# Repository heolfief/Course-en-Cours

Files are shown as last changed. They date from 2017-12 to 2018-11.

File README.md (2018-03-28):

<p align="center">
	<a target="_blank" href="http://www.course-en-cours.com/">
		
	</a>

<h1 align="center">Course en cours</h1>

<p align="center">
	<a target="_blank" href="http://www.course-en-cours.com/">www.course-en-cours.com</a>
</p>
</p>
<HR>
<br>

<p align="center">
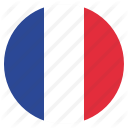
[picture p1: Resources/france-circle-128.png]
	
	<a target="_blank" href="https://github.com/heolfief/Course-en-Cours/blob/master/README_FR.md">VERSION EN FRANCAIS / FRENCH VERSION</a>
</p>

## Table of contents

- [Description](#description)
- [Where to start](#where-to-start)
- [Hardware](#hardware)
- [Software](#software)
- [Creators](#creators)
- [Copyright and license](#copyright-and-license)

## Description

This project contains hardware, software and documentation files for the "course en cours" **educationnal competition in France**.
During a year, teams of 4 to 6 middle/high school **students build their small electic car** using the same tools as engineers. the contest consists of **designing, creating, testing and running** a small model car during the **regional competitions**, to acces the **national final**.

We are two university students in electrical engineering and industrial data processing, from <a href="https://iut-rennes.univ-rennes1.fr/les-6-departements/genie-electrique-informatique-industrielle">IUT de Rennes</a>, France.
Our project is to **integrate embedded telemetry, datalogging and manual control** into the existings cars engines.
We choosed to works with the **Arduino environnement**, to make it possible for everybody to program their car, modify it as they like, and to make programming accesible for the young people of the competition.

This project is **realesed under the general public license and is strongly welcome to modifications**.

## Where to start

In order to be able to program your board with the arduino IDE via usb, you will first need to install a bootloader on your board. Find insruction on how to do that in the <a href="#bootloader">software section</a>.

When this step is done you should be able to programm your board like if it was an arduinon pro mini.

Just install the course-en-cours library (<a href="#software">link in the software section</a>) and import it to your arduino sketch.
<a target="_blank" href="https://www.arduino.cc/en/Guide/Libraries">Here is a tutorial</a> if you need help for this step.

You should now be able to program your board via USB, as described in the <a href="#software">software section</a>.

## Hardware

The hardware is based on 4 main components:
- ATmega328p microcontroller (the same as the arduino uno/nano/pro mini)
- MPU6050 accelerometer and gyro chip
- A FTDI chip (to program the microcontroller via USB)
- A micro SD card holder

This board is **fully arduino compatible** and should be selected in the arduino environnement as the arduino pro mini (ATmega328p, 3.3V 8MHz).

### Documents availables

- <a target="_blank" href="https://github.com/heolfief/Course-en-Cours/blob/master/Hardware/Schematics.pdf">Schematics (PDF)</a>
- <a target="_blank" href="https://github.com/heolfief/Course-en-Cours/blob/master/Hardware/BOM.pdf">Bill of materials (PDF)</a>
- <a target="_blank" href="https://github.com/heolfief/Course-en-Cours/blob/master/Hardware/Carte%20course%20en%20cours.sch">Autodesk Eagle schematics file</a>
- <a target="_blank" href="https://github.com/heolfief/Course-en-Cours/blob/master/Hardware/Carte%20course%20en%20cours.brd">Autodesk Eagle board file</a>
- <a href="https://github.com/heolfief/Course-en-Cours/blob/master/Hardware/Gerbers.zip">Gerber files</a>

### Board form factor
<table border="0">
	<tbody>
		<tr>
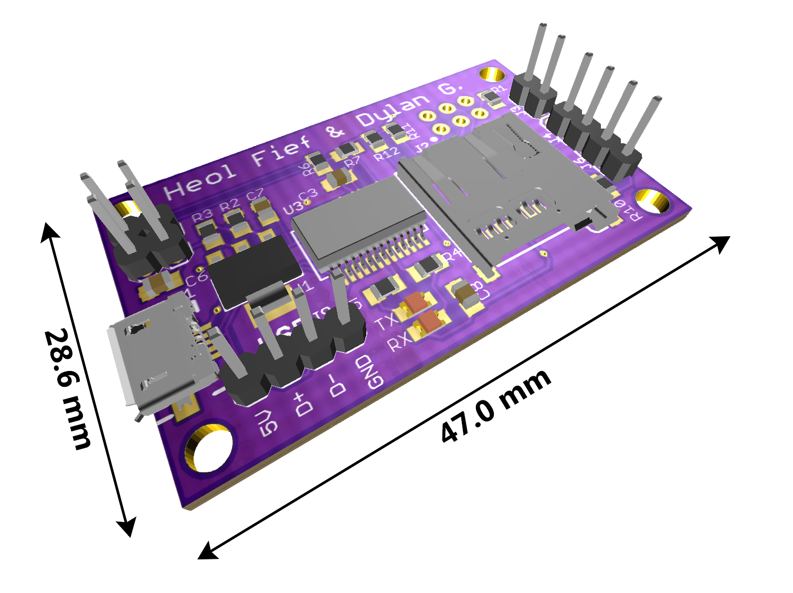
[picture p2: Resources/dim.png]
			<th align="center"></th>
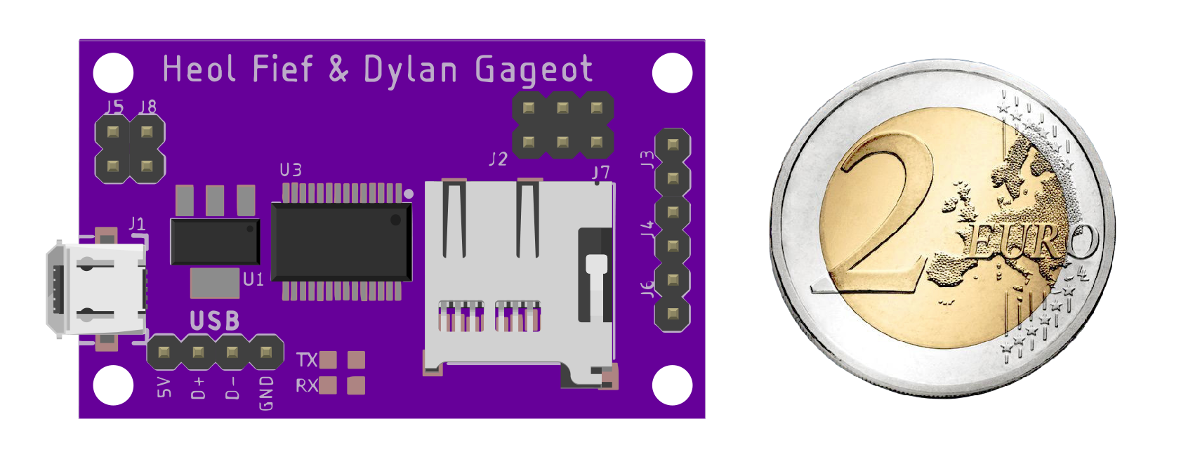
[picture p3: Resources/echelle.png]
			<th align="center"></th>
		</tr>
	</tbody>
</table>

### PCB pinout diagram:
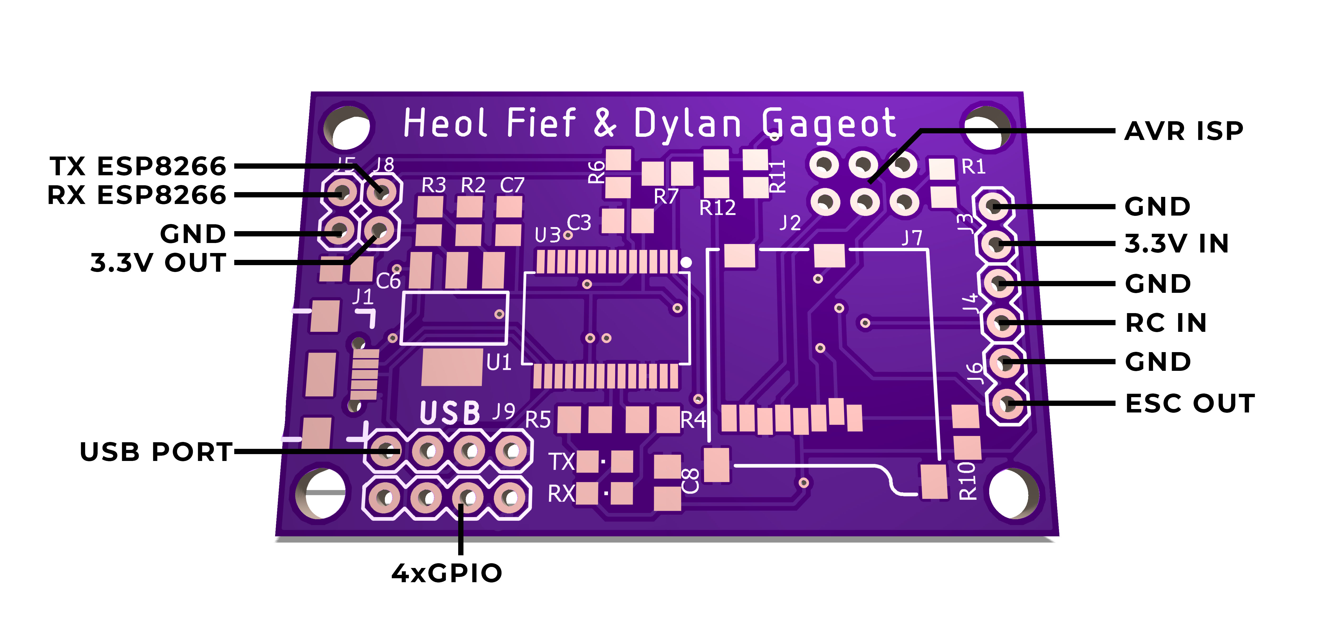
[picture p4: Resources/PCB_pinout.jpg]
PCB pinout


### PCB wiring diagram:
<p align="center">
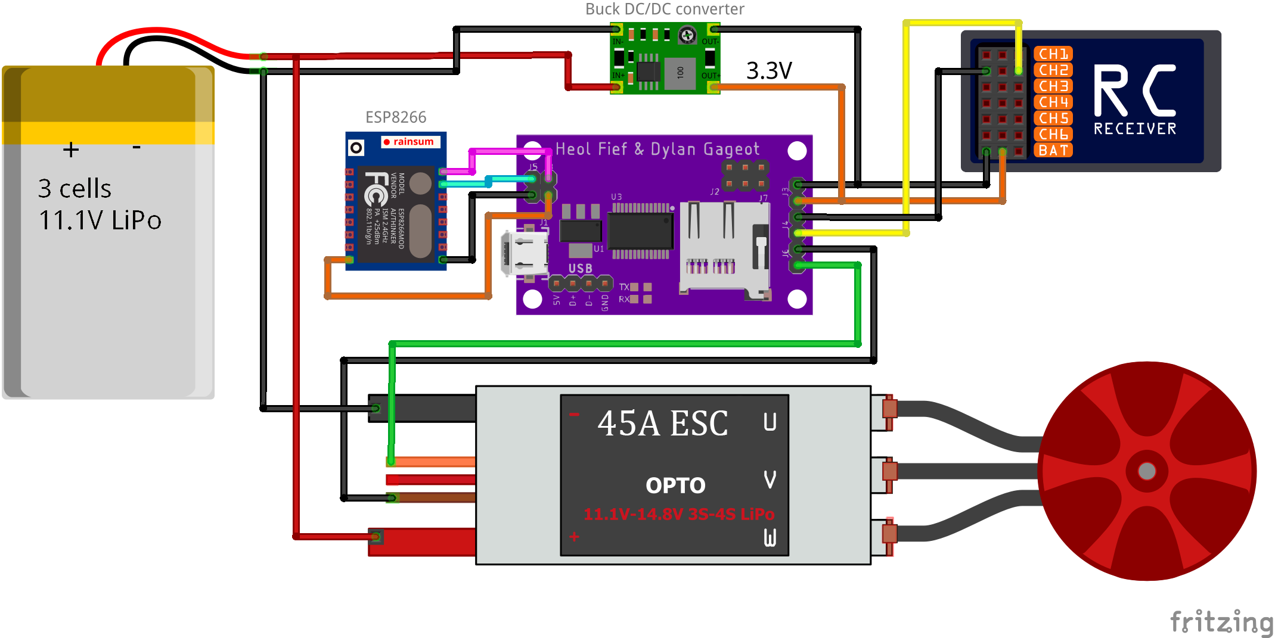
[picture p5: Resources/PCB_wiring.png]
  
</p>

**BE CAREFULL: You need to provide 3.3V to the board, plugging directly the 11.1V LiPo battery will kill it. You can step down the battery voltage with a standard DC/DC converter (also known as buck-converter) set to output 3.3V (min 200mA), like in the wiring diagram above.**

## Software

### Firmware


You can program your course en cours board in C/C++ directly with the <a target="_blank" href="https://www.arduino.cc/en/main/software">arduino IDE</a> via USB, assuming you already have a bootloader installed on your board. Instructions on how to flash a bootloader <a href="#bootloader">below</a>.

In the arduino IDE, select the "arduino pro mini" under Tools/Board, and the ATmega328p 3.3V 8MHz under Tools/Processor. Then select the COM port (under Tools/Port) on wich the board is plugged.
To access all the course en cours related function, just import the "course_en_cours" library to your sketch.
<a target="_blank" href="https://www.arduino.cc/en/Guide/Libraries">Here is a tutorial</a> if you need help for this step.

You should now be able to program your board with the arduino software environement.

The delay() function from the Arduino IDE shouldn't be used in your program because it will block the process of our library.

#### Needed libraries

- [MPU6050](https://github.com/jarzebski/Arduino-MPU6050) by **_jarzebski_** : Allows us to use the IMU.
- [SDFat](https://github.com/greiman/SdFat) by **_greiman_** : Allows us to get a high speed SD card communication.

#### Exemple code:
```cpp
#include "Course_en_Cours.h"

Couse_en_Cours cec;	 // create Couse_en_Cours object

void setup() {
	cec.initialiser(AUTO);
	cec.palier_moteur(1000,0);
	cec.palier_moteur(5000,50);
	cec.palier_moteur(7500,75);
}

void loop() {
	cec.executer();
}
```
<table>
	<tbody>
		<tr>
			<th align="center">Function</th>
			<th align="center">Description</th>
			<th align="center">Parameters</th>
		</tr>
		<tr>
			<td><code>cec.executer(void);</code></td>
			<td>Mandatory function, needs to be run in the loop().</td>
			<td>
				<ul>
				<li><strong>cec</strong> : a variable of type Course_en_cours</li>
				</ul>
			</td>
		</tr>
		<tr>
			<td><code>cec.initialiser(bool pilotage_mode);</code></td>
			<td>Function to set the driving mode. Needs to be run in the setup().</td>
			<td>
				<ul>
				<li><strong>cec</strong> : a variable of type Course_en_cours</li>
				<li><strong>pilotage_mode</strong> : the mode you want your car to run in. Can be set to "AUTO" or "MANU".
					<ul>
						<li>AUTO : you can drive the motor within your arduino code with the palier_moteur function.</li>
						<li>MANU : palier_moteur functions are disabled, and remote control signal is redirected to the ESC. You can manualy drive the motors with a remote.</li>
					</ul>
				</li>
				</ul>
			</td>
		</tr>
		<tr>
			<td><code>cec.palier_moteur(unsigned int ms, unsigned char pourcentage);</code></td>
			<td>The motor power step function. Use it in the setup() to set a fixed power/speed to the motor at a certain time. Can be called several times to create differents steps at different times. </td>
			<td>
				<ul>
					<li><strong>cec</strong> : a variable of type Course_en_cours</li>
					<li><strong>ms</strong> : the time in milieconds you want the function to take effect. Timer starts right after power-up.</li>
					<li><strong>pourcentage</strong> : this sets the power/speed of the motor, in percentage.</li>
				</ul>
			</td>
		</tr>
	</tbody>
</table>

#### Known issues

The actual software have some issues :
- If the .csv file is not already on the SD card, the logging would be slower than expected. Make sure that the file already exists on the card.
- The logging time may vary depending of how many steps (palier_moteur functions) you have added.
- The object Course_en_Cours must be called "cec" and declared as global variable (away from the loop() and setup(), or from any fonction).

### Bootloader

In order to be able to program your board with the arduino IDE via usb, you will first need to install a bootloader on your board. Sparkfun have made an easy to understand tutorial on how to do that here : <a target="_blank" href="https://learn.sparkfun.com/tutorials/installing-an-arduino-bootloader">Installing an arduino bootloader</a>

Here is the wiring diagram to install the bootloader with an arduino UNO (follow the sparkfun tutorial for step by step instructions).

<p align="center">
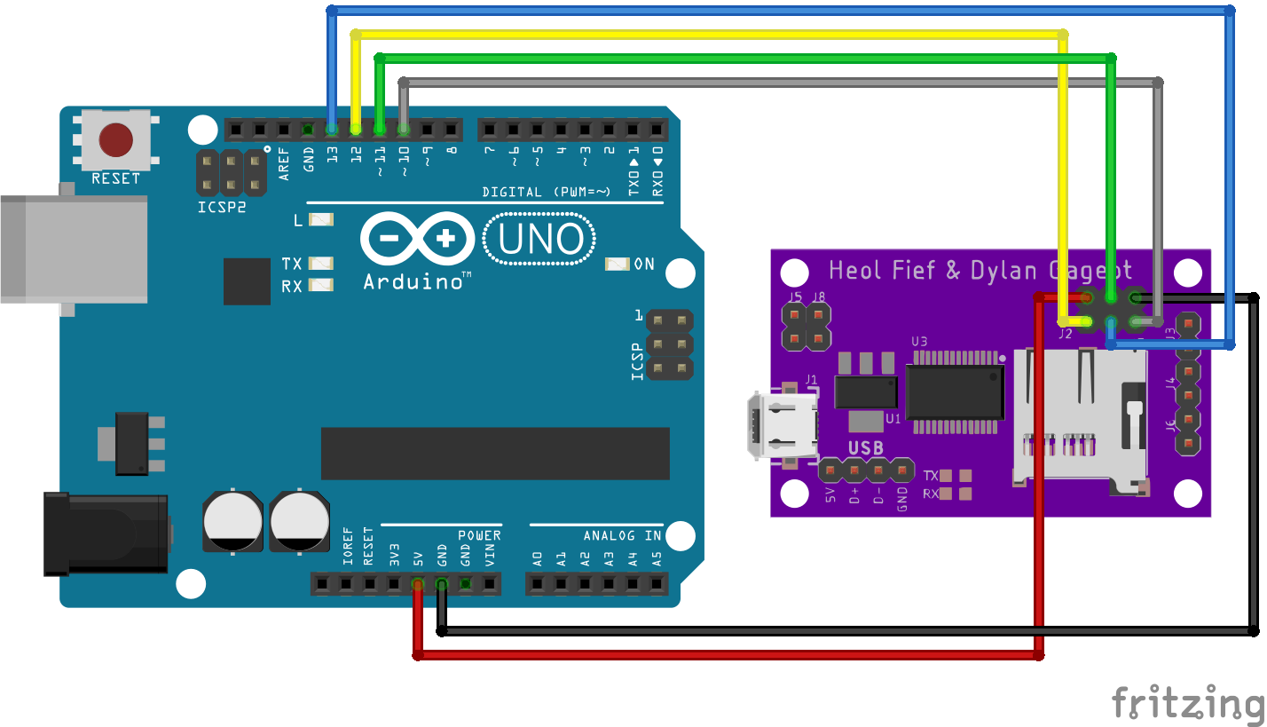
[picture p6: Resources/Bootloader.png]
  
</p>

When installing the bootloader, make sure your arduino target board is the arduino pro mini (ATmega328p 3.3V 8MHz), as this board is arduino pro mini compatible.

You should now be able to program your board via USB, as described in the <a href="#software">software section</a>.

## Creators

**Heol Fief**

- <https://github.com/heolfief>

**Dylan Gageot**

- <https://github.com/dylangageot>

## Copyright and license
heolfief/Course-en-Cours is licensed under the GNU General Public License v3.0.

See the <a target="_blank" href="https://github.com/heolfief/Course-en-Cours/blob/master/LICENSE">LICENSE file</a> for more informations.

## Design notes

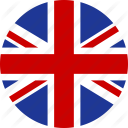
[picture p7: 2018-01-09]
Resources/england-circle-128.png

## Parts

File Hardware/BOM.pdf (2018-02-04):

Qty Value | Device | Package | Parts | Description | Price (on 100pcs order) DIGIKEY | Total price
1 | 1.6k | R-EU_R0805 | R0805 | R2 | Resistor | 0,003 € | 0,003 €
5 | 100k | R-EU_R0805 | R0805 | R1, R6, R7, R10, R11, R12 | Resistor | 0,003 € | 0,015 €
1 | 1k | R-EU_R0805 | R0805 | R3 | Resistor | 0,003 € | 0,003 €
2 | 4.7k | R-EU_R0805 | R0805 | R8, R9 | Resistor | 0,003 € | 0,006 €
2 | 330 | R-EU_R0805 | R0805 | R4, R5 | Resistor | 0,003 € | 0,006 €
6 | 100n | C-EUC0805 | C0805 | C3, C4, C5, C8, C9, C10 | Capacitor | 0,010 € | 0,060 €
1 | 10n | C-EUC0805 | C0805 | C12 | Capacitor | 0,010 € | 0,010 €
1 | 1u | C-EUC0805 | C0805 | C7 | Capacitor | 0,010 € | 0,010 €
1 | 2.2n | C-EUC0805 | C0805 | C11 | Capacitor | 0,010 € | 0,010 €
2 | 22p | C-EUC0805 | C0805 | C1, C2 | Capacitor | 0,010 € | 0,020 €
1 | 4.7u | C-EUC0805 | C0805 | C6 | Capacitor | 0,050 € | 0,050 €
2 | | LEDCHIPLED_0805 | CHIPLED_0805 | RX, TX | LED | 0,080 € | 0,160 €
1 | 8MHz | CRYSTAL-8MHZSMD-5X3.2 | CRYSTAL-SMD-5X3.2-4PAD | Y1 | 8MHz Crystal | 0,500 € | 0,500 €
1 | V_REG_317SMD | V_REG_317SMD | SOT223 | U1 | Voltage Regulator | 0,600 € | 0,600 €
1 | ATMEGA328P_TQFP | ATMEGA328P_TQFP | TQFP32-08 | U2 | Popular 328P in QFP | 1,500 € | 1,500 €
1 | FT232RL | FT232RL-BASICSSOP | SSOP28DB | U3 | FT232RL USB UART | 3,700 € | 3,700 €
1 | MPU6050 | MPU6050 | HVQFN24_NS | U4 | 6-Axis Motion Sensor | 2,920 € | 2,920 €
5 | | CONN_02 | 1X02 | J3, J4, J5, J6, J8 | Standard 0.1" header | 0,100 € | 0,500 €
1 | | CONN_04 | 1X04 | J9 | Standard 0.1" header | 0,100 € | 0,100 €
1 | | USB_MICRO-B_FEMALE-SMT | USB-B-MICRO-SMD | J1 | USB Type Micro-B Connector | 0,300 € | 0,300 €
1 | MICRO-SD_CARD_SOCKET MICRO-SD_CARD_SOCKET | MICRO-SD-SOCKET | J7 | Micro SD socket | 2,000 € | 2,000 €
| | | | | TOTAL/carte | | 12,47 €

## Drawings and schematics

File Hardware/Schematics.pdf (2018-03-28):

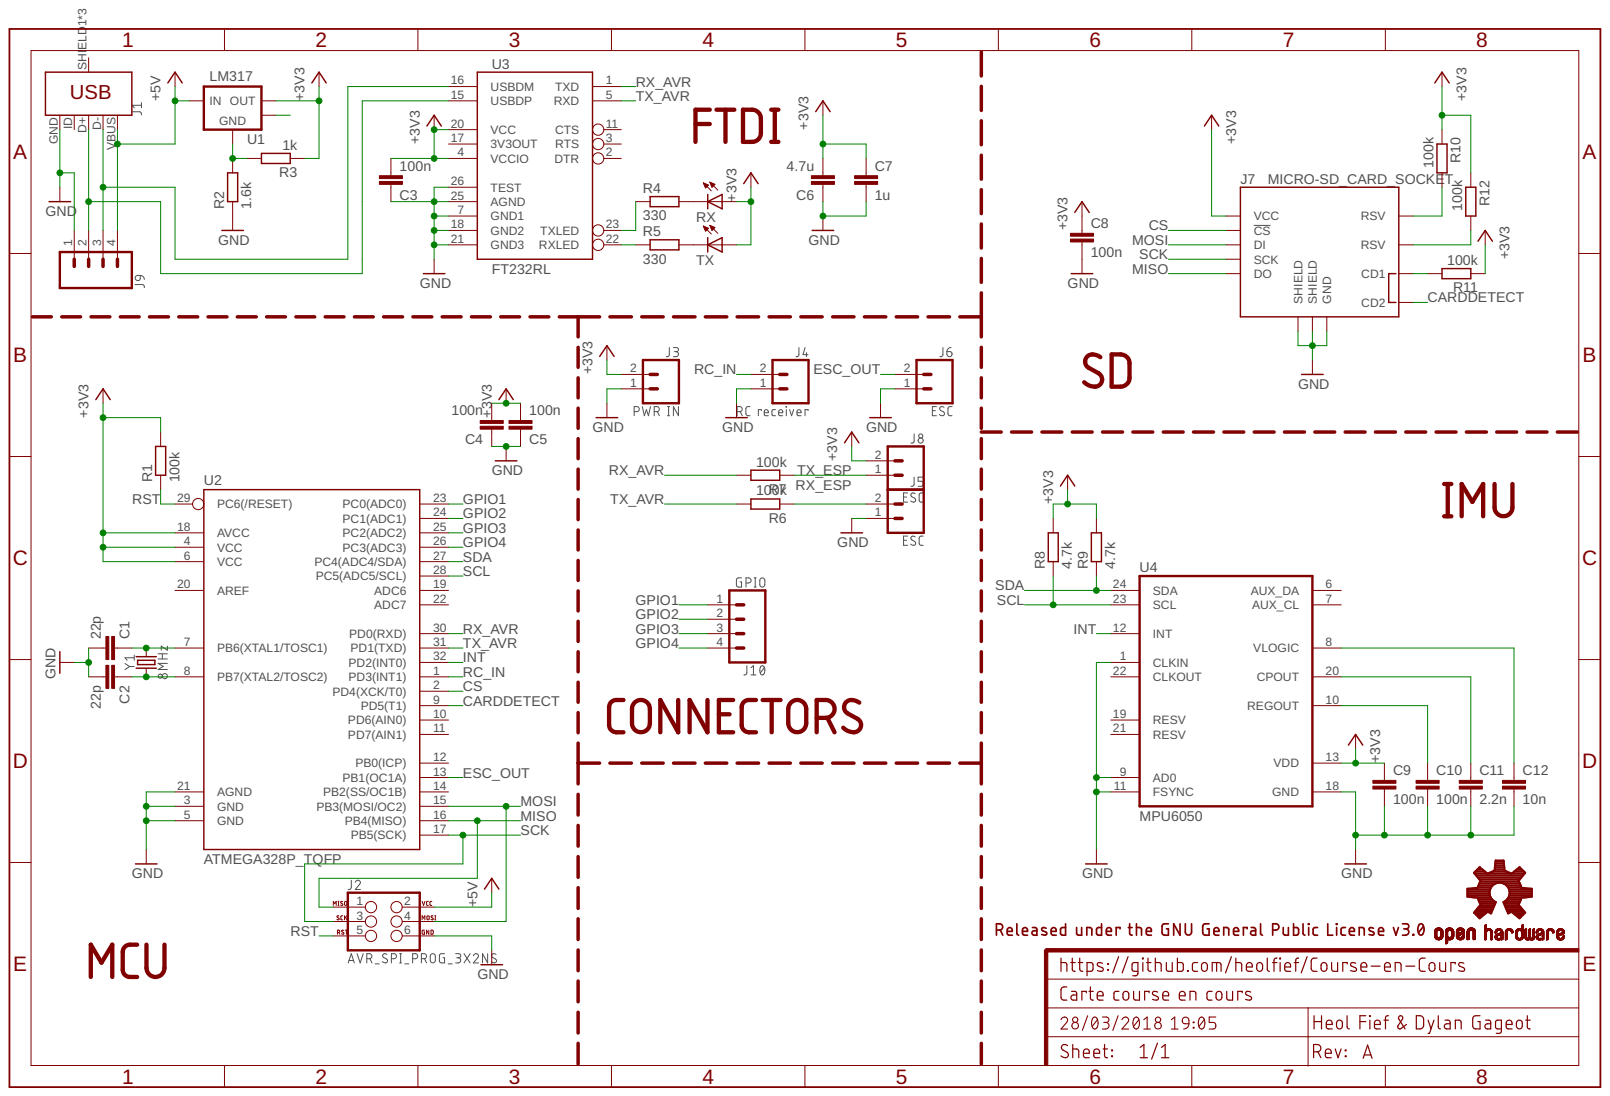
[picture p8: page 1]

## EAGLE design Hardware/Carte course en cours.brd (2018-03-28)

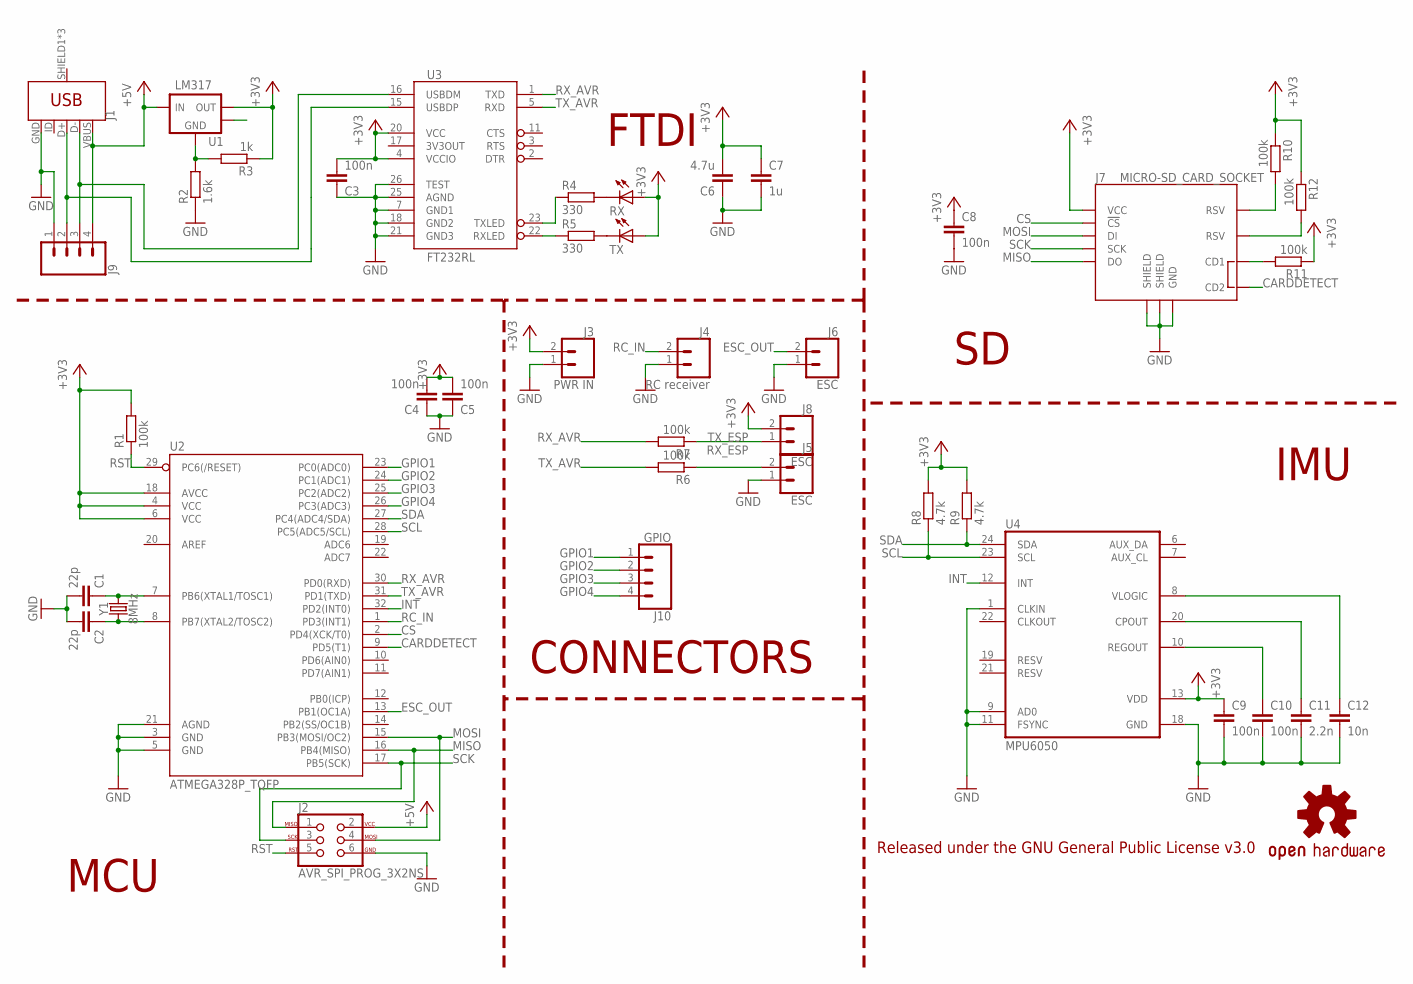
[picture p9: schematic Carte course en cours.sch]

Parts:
C1, C2: 22p; C0805
C3, C4, C5, C8, C9, C10: 100n; C0805
C6: 4.7u; C0805
C7: 1u; C0805
C11: 2.2n; C0805
C12: 10n; C0805
J1: USB_MICRO-B_FEMALE-SMT; USB-B-MICRO-SMD
J2: AVR_SPI_PROG_3X2NS; 2X3-NS
J3: PWR IN; 1X02
J4: RC receiver; 1X02
J5, J6, J8: ESC; 1X02
J7: MICRO-SD_CARD_SOCKET; MICRO-SD-SOCKET
J9: CONN_04; 1X04
J10: GPIO; 1X04
LOGO1: OSHW-LOGOM; OSHW-LOGO-M
R1, R6, R7, R10, R11, R12: 100k; R0805
R2: 1.6k; R0805
R3: 1k; R0805
R4, R5: 330; R0805
R8, R9: 4.7k; R0805
RX: LEDCHIPLED_0805; CHIPLED_0805
TX: LEDCHIPLED_0805; CHIPLED_0805
U1: LM317; SOT-223-3
U2: ATMEGA328P_TQFP; TQFP32-08
U3: FT232RL; SSOP28DB
U4: MPU6050; HVQFN24_NS
Y1: 8MHz; CRYSTAL-SMD-5X3.2-4PAD

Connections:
+3V3: C3.2, C4.2, C5.2, C6.2, C7.1, C8.1, C9.1, J3.2, J7.VCC, J8.2, R1.2, R3.1, R8.2, R9.2, R10.1, R11.1, R12.1, RX.A, TX.A, U1.2 (VOUT), U2.4 (VCC), U2.6 (VCC), U2.18 (AVCC), U3.4 (VCCIO), U3.20 (VCC), U4.13 (VDD)
+5V: J1.VBUS, J2.2, J9.4, U1.3 (VIN)
CARDDETECT: J7.CD2, U2.9 (PD5(T1))
CS: J7.CS (!CS), U2.2 (PD4(XCK/T0))
ESC_OUT: J6.2, U2.13 (PB1(OC1A))
GND: C1.2, C2.2, C3.1, C4.1, C5.1, C6.1, C7.2, C8.2, C9.2, C10.2, C11.2, C12.2, J1.GND, J2.6, J3.1, J4.1, J5.1, J6.1, J7.GND, J7.GND1 (SHIELD), J7.GND3 (SHIELD), J9.1, R2.1, U2.3 (GND), U2.5 (GND), U2.21 (AGND), U3.7 (GND1), U3.18 (GND2), U3.21 (GND3), U3.25 (AGND), U3.26 (TEST), U4.1 (CLKIN), U4.9 (AD0), U4.11 (FSYNC), U4.18 (GND)
GPIO1: J10.1, U2.23 (PC0(ADC0))
GPIO2: J10.2, U2.24 (PC1(ADC1))
GPIO3: J10.3, U2.25 (PC2(ADC2))
GPIO4: J10.4, U2.26 (PC3(ADC3))
HEATSINK: U1.4 (HEATSINK)
INT: U2.32 (PD2(INT0)), U4.12 (INT)
MISO: J2.1, J7.DO, U2.16 (PB4(MISO))
MOSI: J2.4, J7.DI, U2.15 (PB3(MOSI/OC2))
unnamed: R2.2, R3.2, U1.1 (GND)
unnamed: J1.D-, J9.3, U3.16 (USBDM)
unnamed: C1.1, U2.7 (PB6(XTAL1/TOSC1)), Y1.3 (2)
unnamed: C2.1, U2.8 (PB7(XTAL2/TOSC2)), Y1.1
unnamed: J1.D+, J9.2, U3.15 (USBDP)
unnamed: C11.1, U4.20 (CPOUT)
unnamed: R4.1, U3.23 (TXLED)
unnamed: R5.1, U3.22 (RXLED)
unnamed: R4.2, RX.C
unnamed: R5.2, TX.C
unnamed: C10.1, U4.10 (REGOUT)
unnamed: C12.1, U4.8 (VLOGIC)
unnamed: J7.RSV1 (RSV), R10.2
unnamed: J7.RSV2 (RSV), R12.2
unnamed: J7.CD1, R11.2
RC_IN: J4.2, U2.1 (PD3(INT1))
RST: J2.5, R1.1, U2.29 (PC6(/RESET))
RX_AVR: R7.2, U2.30 (PD0(RXD)), U3.1 (TXD)
RX_ESP: J5.2, R6.1
SCK: J2.3, J7.SCLK (SCK), U2.17 (PB5(SCK))
SCL: R8.1, U2.28 (PC5(ADC5/SCL)), U4.23 (SCL)
SDA: R9.1, U2.27 (PC4(ADC4/SDA)), U4.24 (SDA)
TX_AVR: R6.2, U2.31 (PD1(TXD)), U3.5 (RXD)
TX_ESP: J8.1, R7.1

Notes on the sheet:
MCU
IMU
FTDI
Released under the GNU General Public License v3.0
CONNECTORS

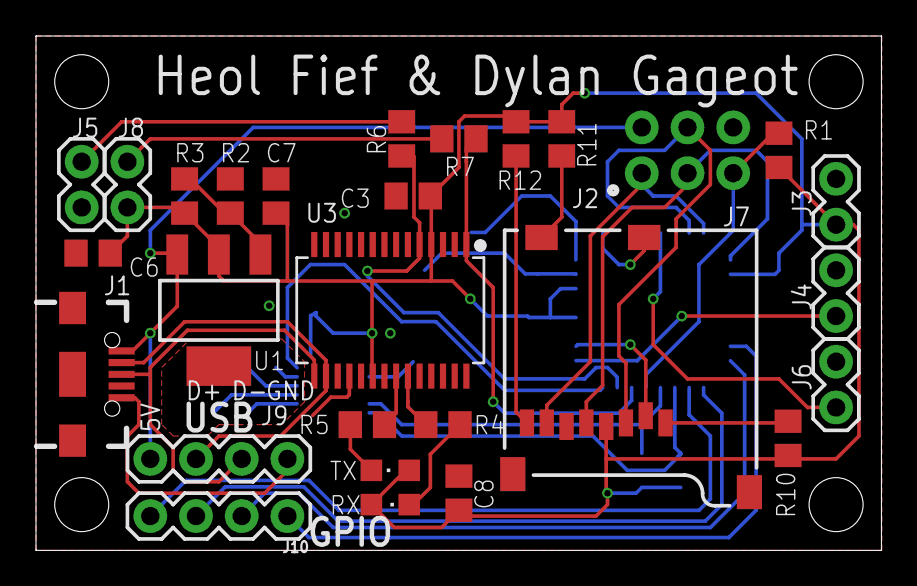
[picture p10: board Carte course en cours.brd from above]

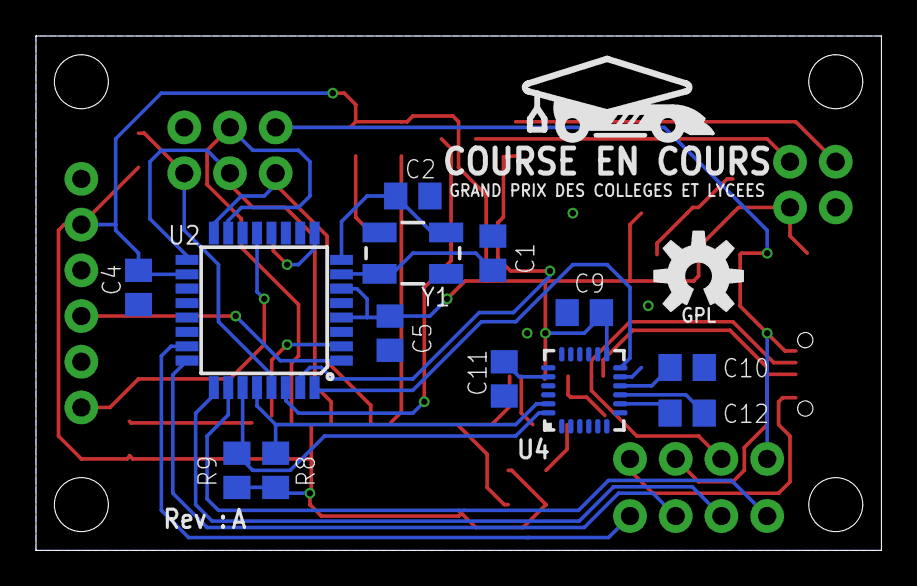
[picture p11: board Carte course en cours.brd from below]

Board: 2 copper layers, 47.0 x 28.6 mm, 42 parts (14 on the bottom side), 37 nets.

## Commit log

2017-11-30 Add Schematics files
    [Carte course en cours.sch]
2017-12-02 Add connectors
    [Carte course en cours.sch]
2017-12-02 Add brd file
    [Carte course en cours.brd, Carte course en cours.sch]
2017-12-05 Place components
    [Carte course en cours.brd, Carte course en cours.sch]
2017-12-06 Add gitignore
    [Carte course en cours.brd, Carte course en cours.sch]
2017-12-09 Add silkscreen
    [Carte course en cours.brd, Carte course en cours.sch]
2017-12-09 Add schematics PDF
2017-12-09 Add BOM
    [BOM.ods]
2017-12-09 Add price to BOM
    [BOM.ods]
2017-12-09 Improce pwr trace lenght
    [Carte course en cours.brd]
2017-12-10 Add heatsink plane
    [Carte course en cours.brd, Carte course en cours.sch]
2017-12-15 Improve trace shape
    [Carte course en cours.brd]
2017-12-15 remove libreoffice file
    [BOM.ods]
2017-12-16 Add fritzing schematics
2017-12-16 Add wiring diagrams
2017-12-16 Add ESC and RC receiver
2017-12-16 Add ESC and RC receiver to wiring diagram
2017-12-16 Add max voltage warning
2017-12-16 Add ISP pin 1 indentifier
    [Carte course en cours.brd]
2017-12-17 Update wiring diagrams
2017-12-21 Update Course_en_Cours.h and .cpp
    The library can be build with the Arduino IDE compiler -> need to test this library on the prototype.
2018-01-14 Add Gerbers
    [Carte course en cours.drills.xln]
2018-02-04 Changed MCU frequency to 8MHz, to run safe at 3.3V
    [Carte course en cours.brd, Carte course en cours.sch]
2018-03-28 Add 4 GPIO
    [Carte course en cours.brd, Carte course en cours.sch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]
2018-11-06 [ImgBot] Optimize images
    *Total -- 1,442.77kb -> 1,224.88kb (15.1%)
    /Resources/PCB_pinout.jpg -- 932.86kb -> 729.86kb (21.76%)
    /Resources/Bootloader.png -- 117.26kb -> 102.45kb (12.63%)
    /Resources/echelle.png -- 392.65kb -> 392.57kb (0.02%)

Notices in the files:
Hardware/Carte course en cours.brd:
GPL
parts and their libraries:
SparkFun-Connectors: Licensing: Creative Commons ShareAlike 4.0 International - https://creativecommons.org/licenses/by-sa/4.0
